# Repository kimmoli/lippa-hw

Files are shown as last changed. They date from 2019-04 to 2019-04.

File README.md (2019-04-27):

LIPPA
=====

* Powering 7.4V 2.5Ah lipo
* PCB Size 80x50 mm, M3 mounting holes at corners 3.5/3.5
* 4 stepper motor drivers
* 3 servo drivers
* CPU STM32
  * UART for Lidar
  * Debug UART
  * USB VCP
  * 3 timers for servo
  * 4 timers for stepper
  * 4 GPIO to control servo directions
  * 4 GPIO to control servo enables
  * 4 GPIO to control servo microstep modes
  * SPI for PS2 controller

Parts
===== 
* CPU [STM32F417VE](http://www.st.com/content/ccc/resource/technical/document/datasheet/98/9f/89/73/01/b1/48/98/DM00035129.pdf/files/DM00035129.pdf/jcr:content/translations/en.DM0003512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)
* Stepper drivers [DRV8834](http://www.ti.com/lit/ds/symlink/drv8834.pdf)
* Power supply [TPS561201](http://www.ti.com/lit/ds/symlink/tps561201.pdf)

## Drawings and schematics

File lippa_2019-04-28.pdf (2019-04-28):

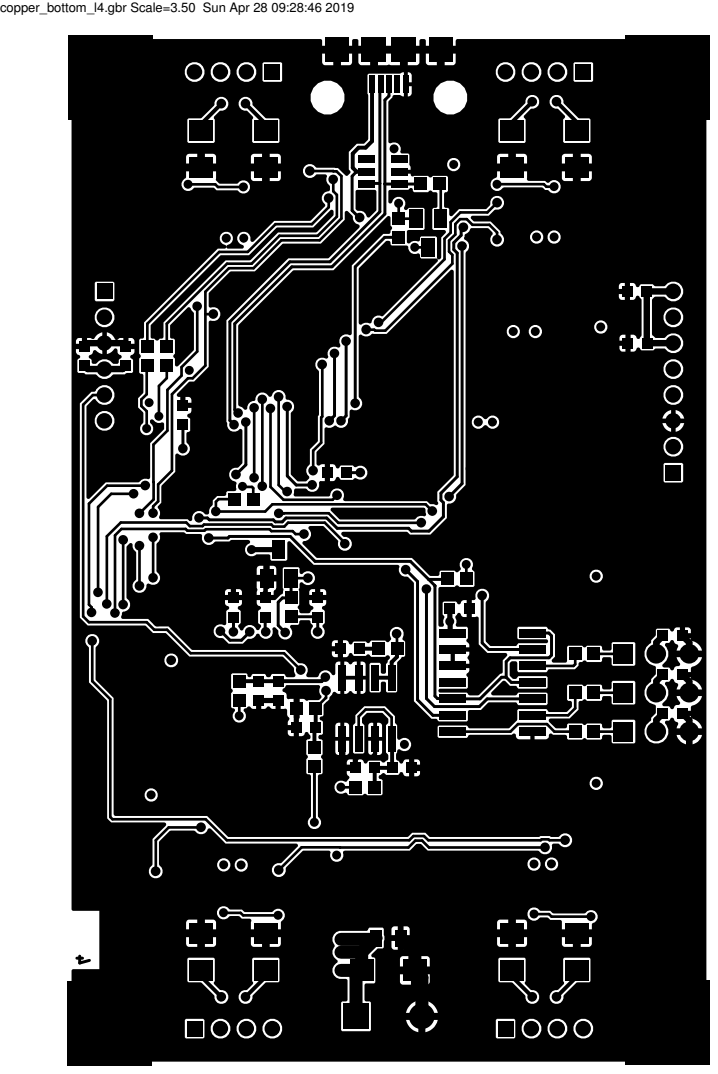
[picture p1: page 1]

copper_bottom_l4.gbr Scale=3.50 Sun Apr 28 09:28:46 2019

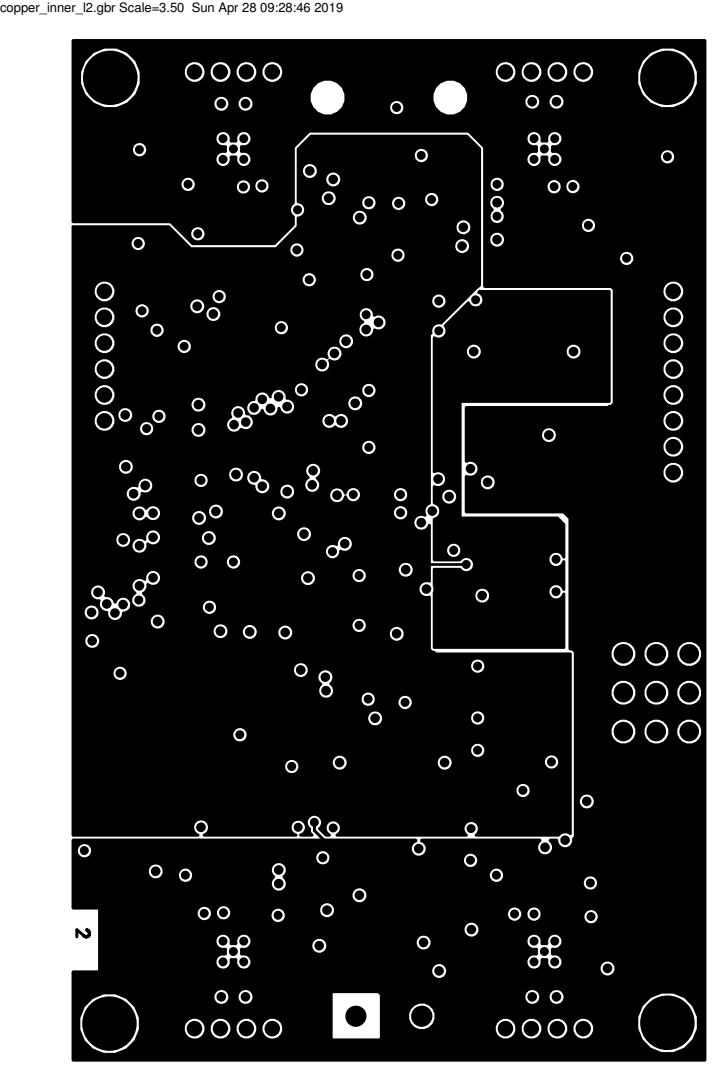
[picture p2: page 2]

copper_inner_l2.gbr Scale=3.50 Sun Apr 28 09:28:46 2019

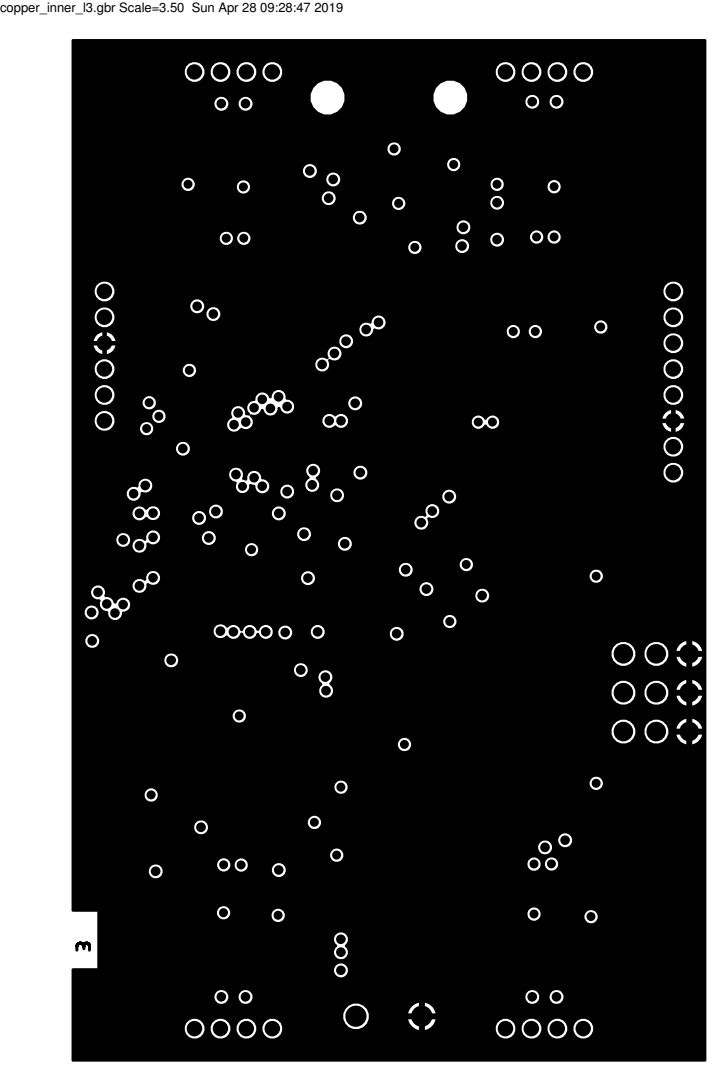
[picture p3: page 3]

copper_inner_l3.gbr Scale=3.50 Sun Apr 28 09:28:47 2019

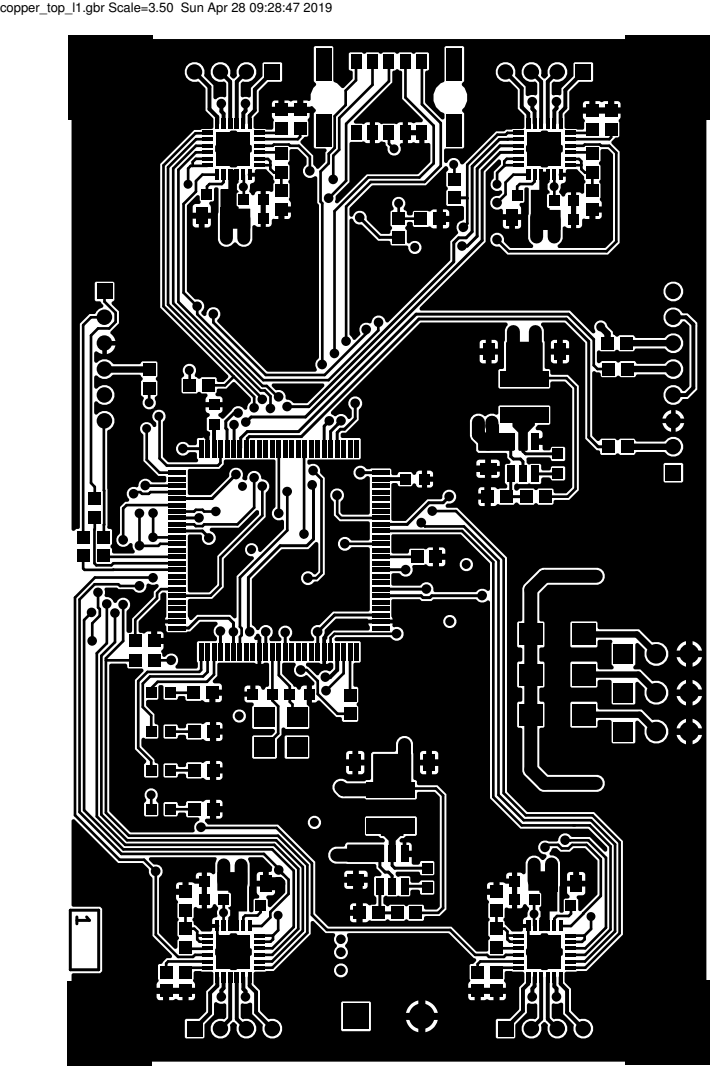
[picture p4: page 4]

copper_top_l1.gbr Scale=3.50 Sun Apr 28 09:28:47 2019

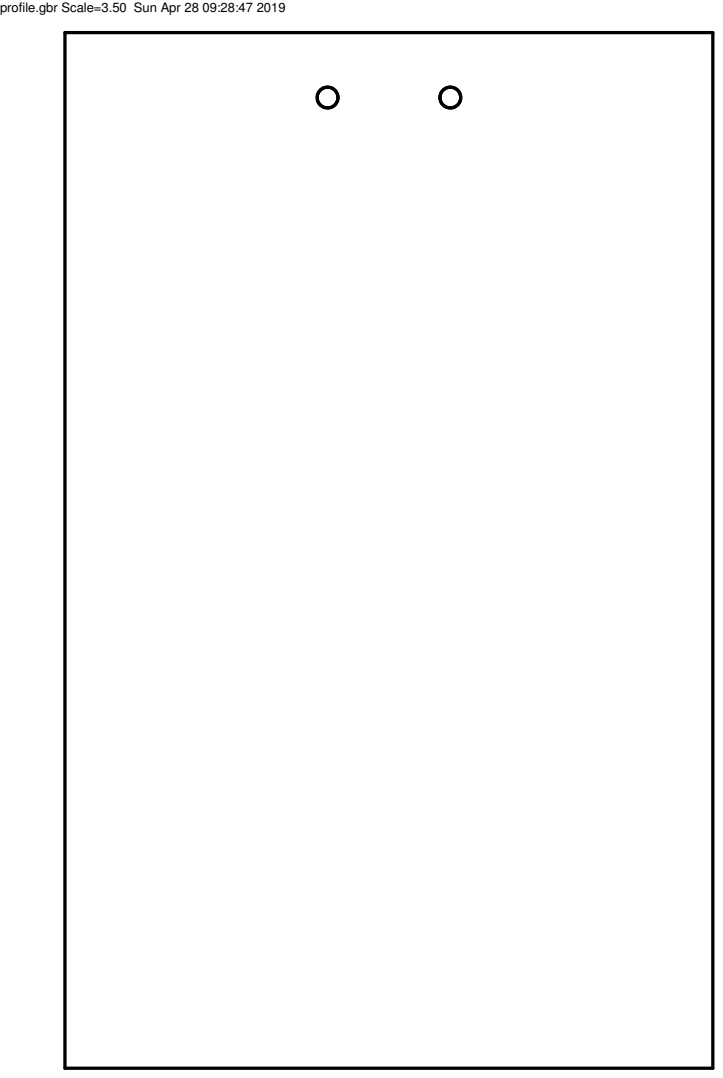
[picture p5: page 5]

profile.gbr Scale=3.50 Sun Apr 28 09:28:47 2019

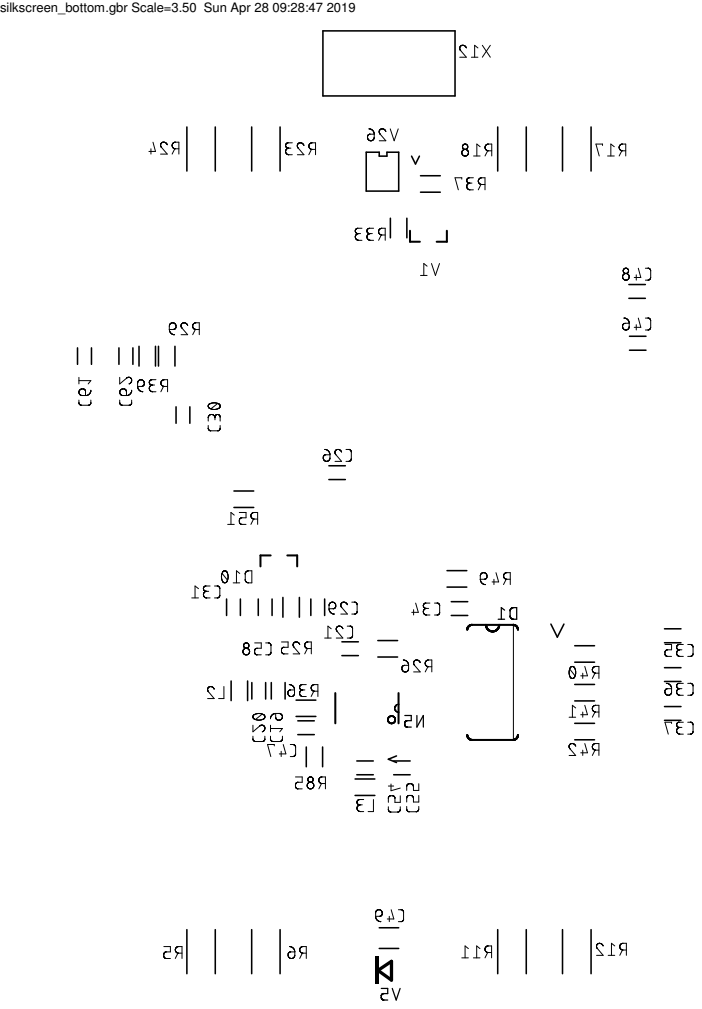
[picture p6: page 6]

silkscreen_bottom.gbr Scale=3.50 Sun Apr 28 09:28:47 2019

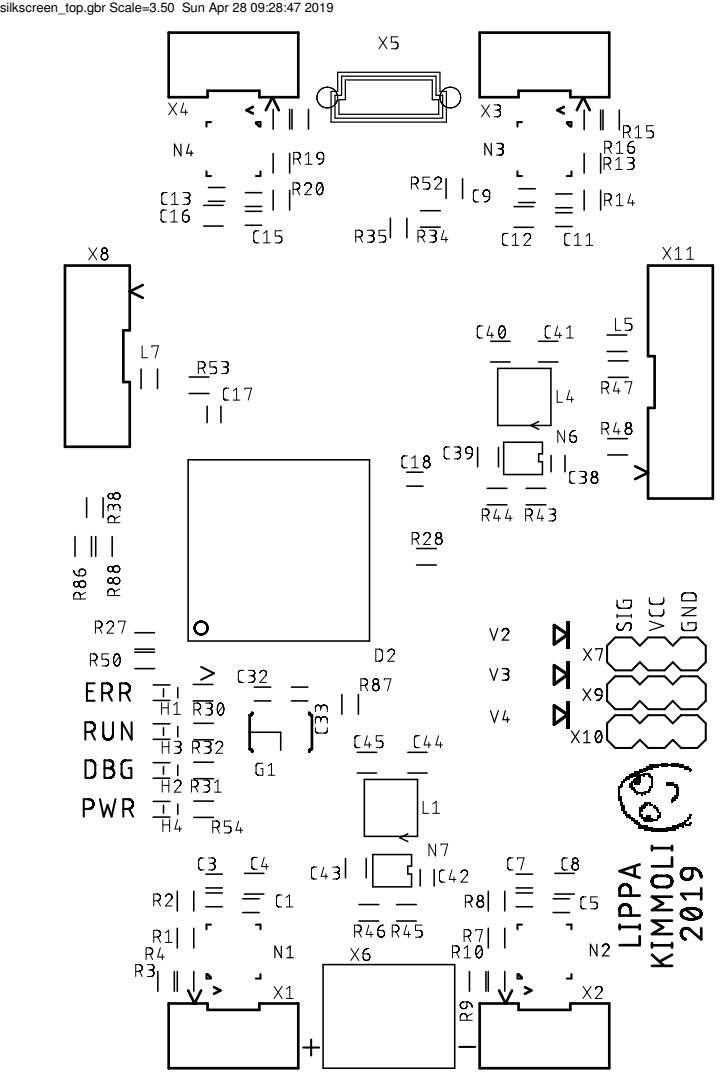
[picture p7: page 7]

silkscreen_top.gbr Scale=3.50 Sun Apr 28 09:28:47 2019

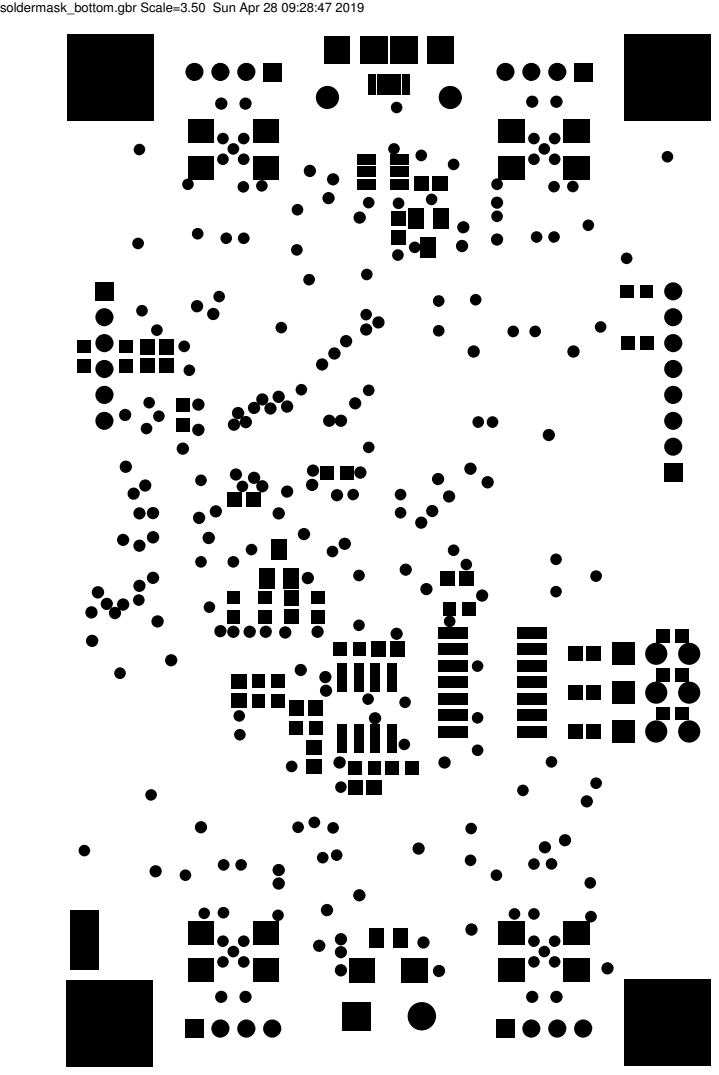
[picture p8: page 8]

soldermask_bottom.gbr Scale=3.50 Sun Apr 28 09:28:47 2019

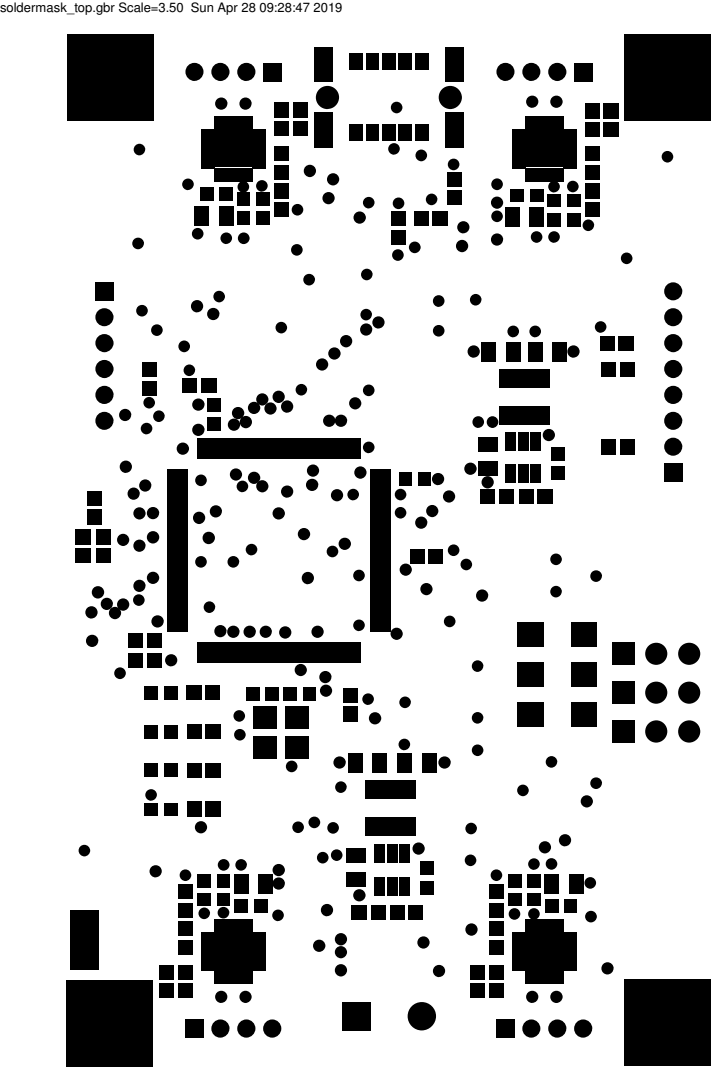
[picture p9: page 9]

soldermask_top.gbr Scale=3.50 Sun Apr 28 09:28:47 2019

solderpaste_bottom.gbr Scale=3.50 Sun Apr 28 09:28:47 2019 solderpaste_top.gbr Scale=3.50 Sun Apr 28 09:28:47 2019

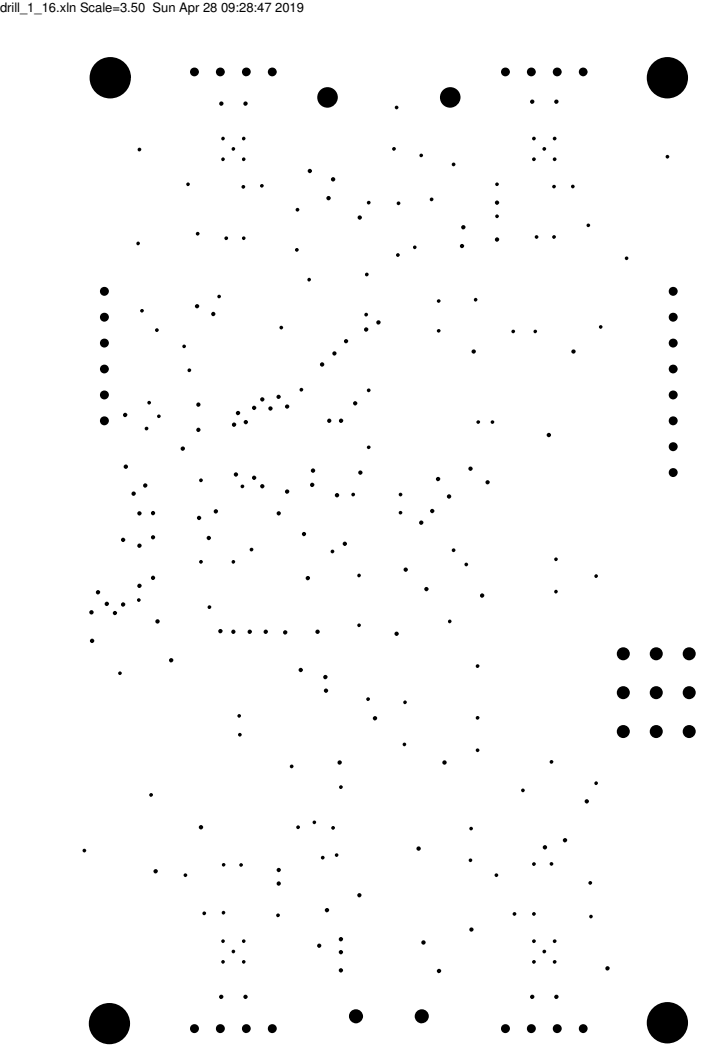
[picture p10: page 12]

drill_1_16.xln Scale=3.50 Sun Apr 28 09:28:47 2019

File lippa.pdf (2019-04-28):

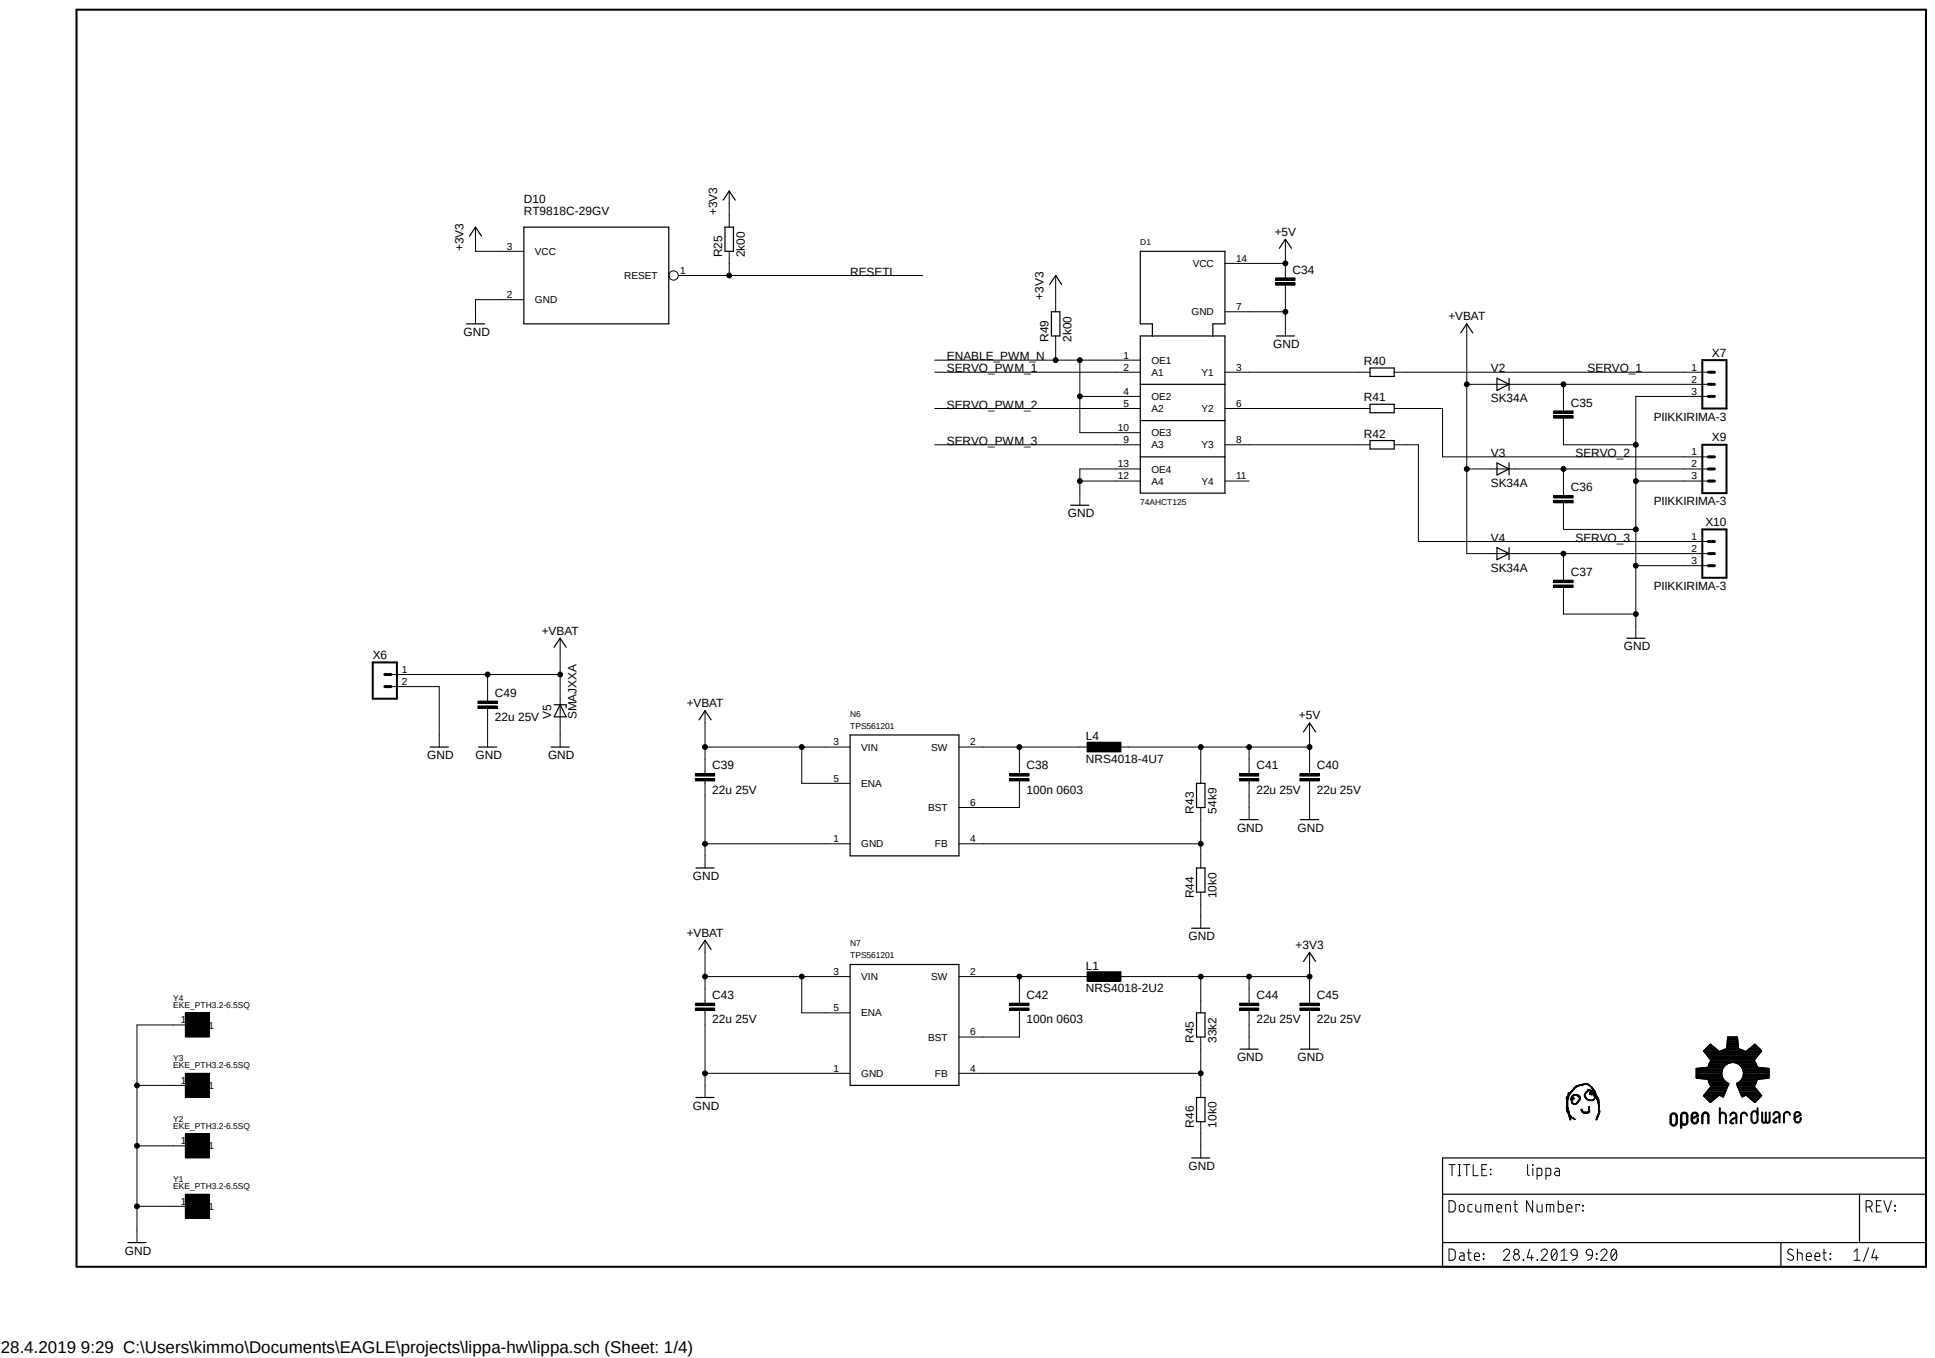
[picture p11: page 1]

28.4.2019 9:29 C:\Users\kimmo\Documents\EAGLE\projects\lippa-hw\lippa.sch (Sheet: 1/4)

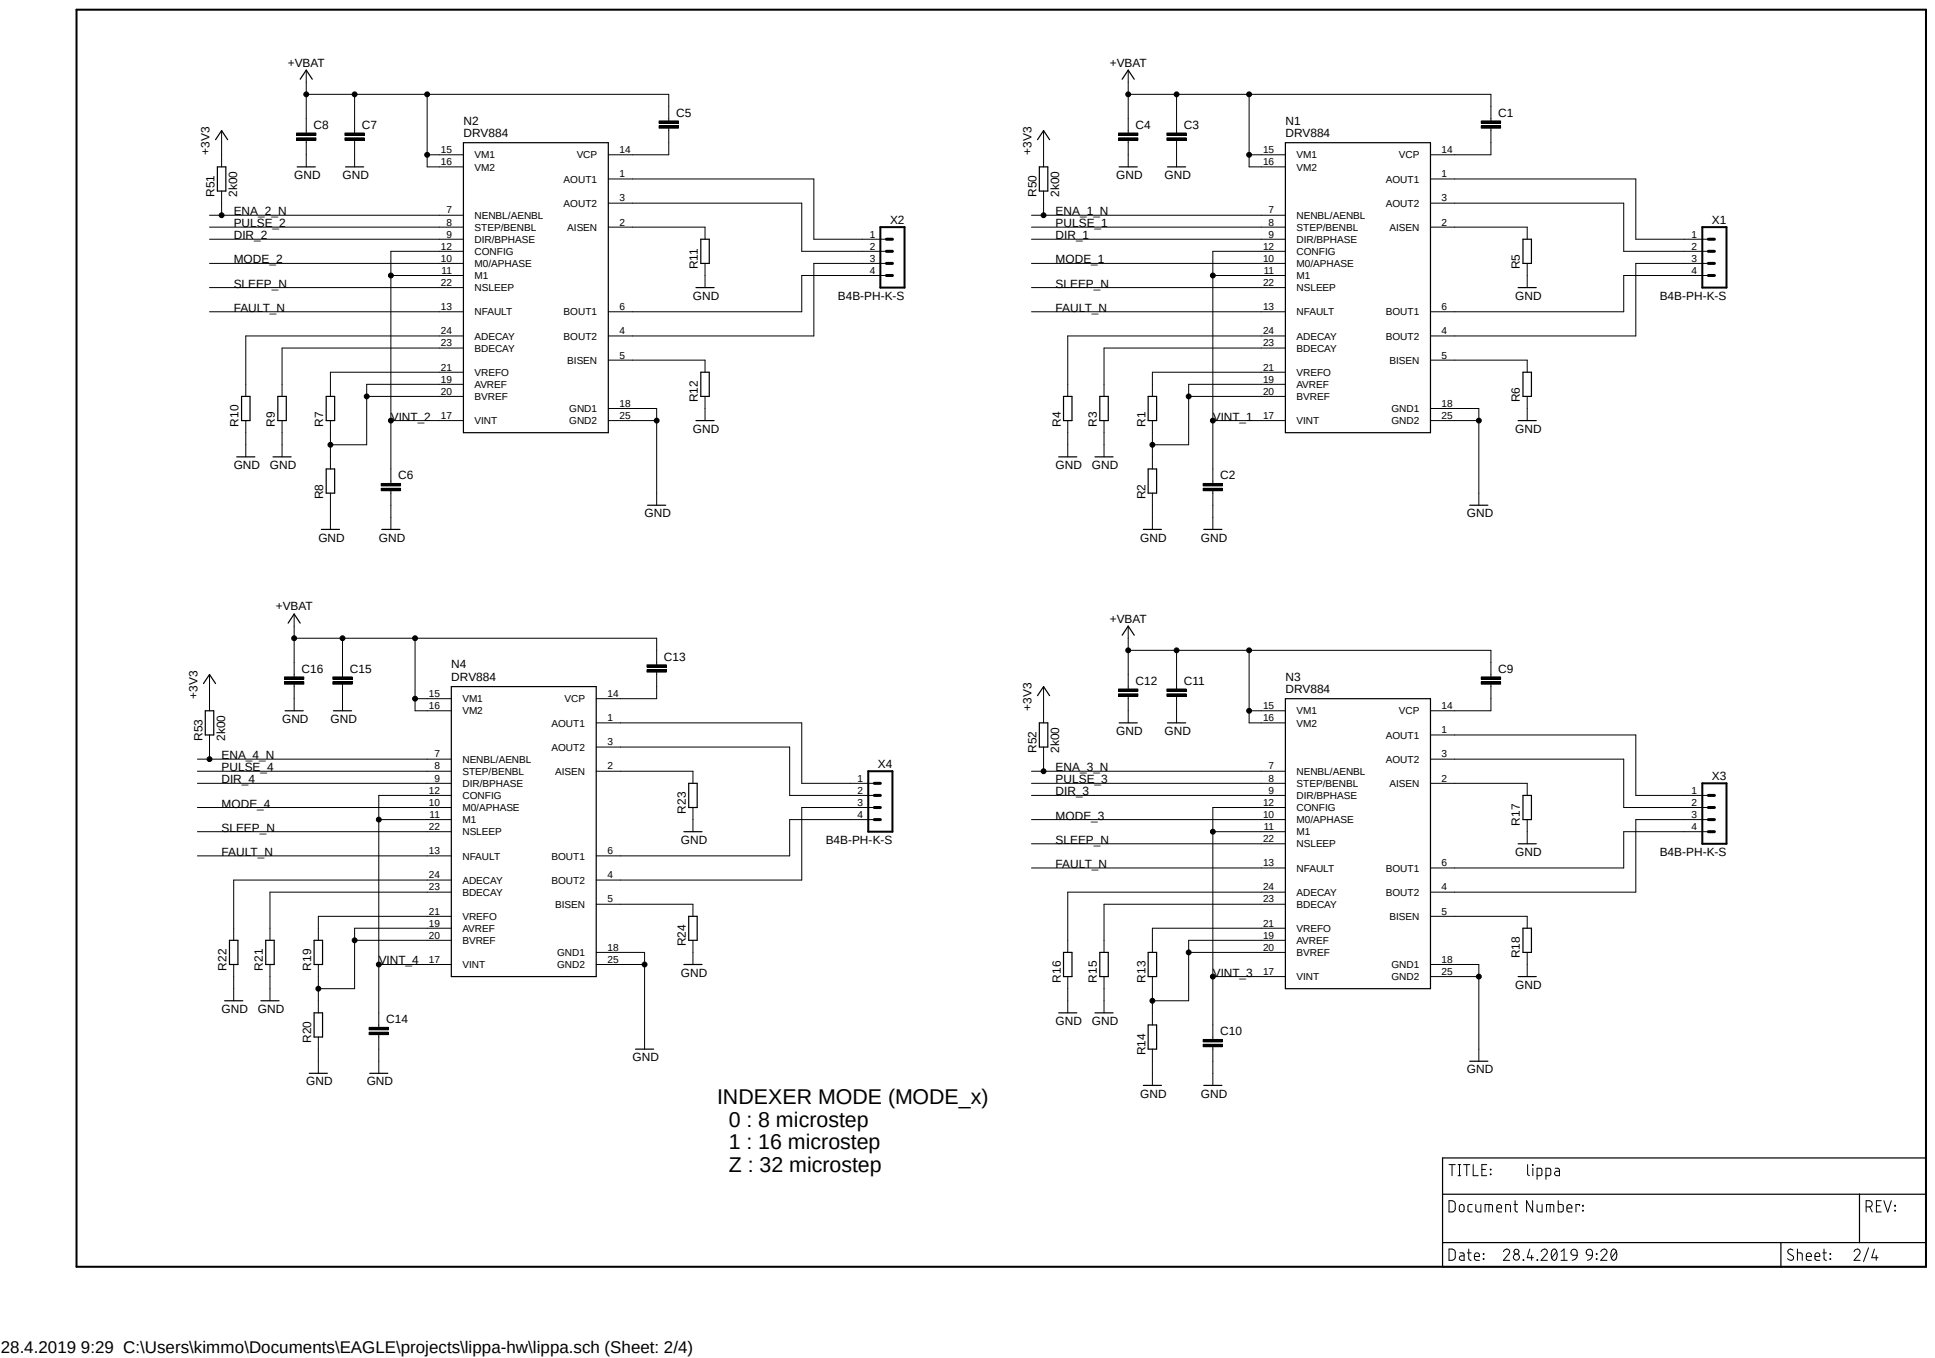
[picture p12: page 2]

BDECAY 23 | 0 : 8 microstep

AVREF 19

VREFO 21

28.4.2019 9:29 C:\Users\kimmo\Documents\EAGLE\projects\lippa-hw\lippa.sch (Sheet: 2/4)


28.4.2019 9:29 C:\Users\kimmo\Documents\EAGLE\projects\lippa-hw\lippa.sch (Sheet: 3/4)


28.4.2019 9:29 C:\Users\kimmo\Documents\EAGLE\projects\lippa-hw\lippa.sch (Sheet: 4/4)

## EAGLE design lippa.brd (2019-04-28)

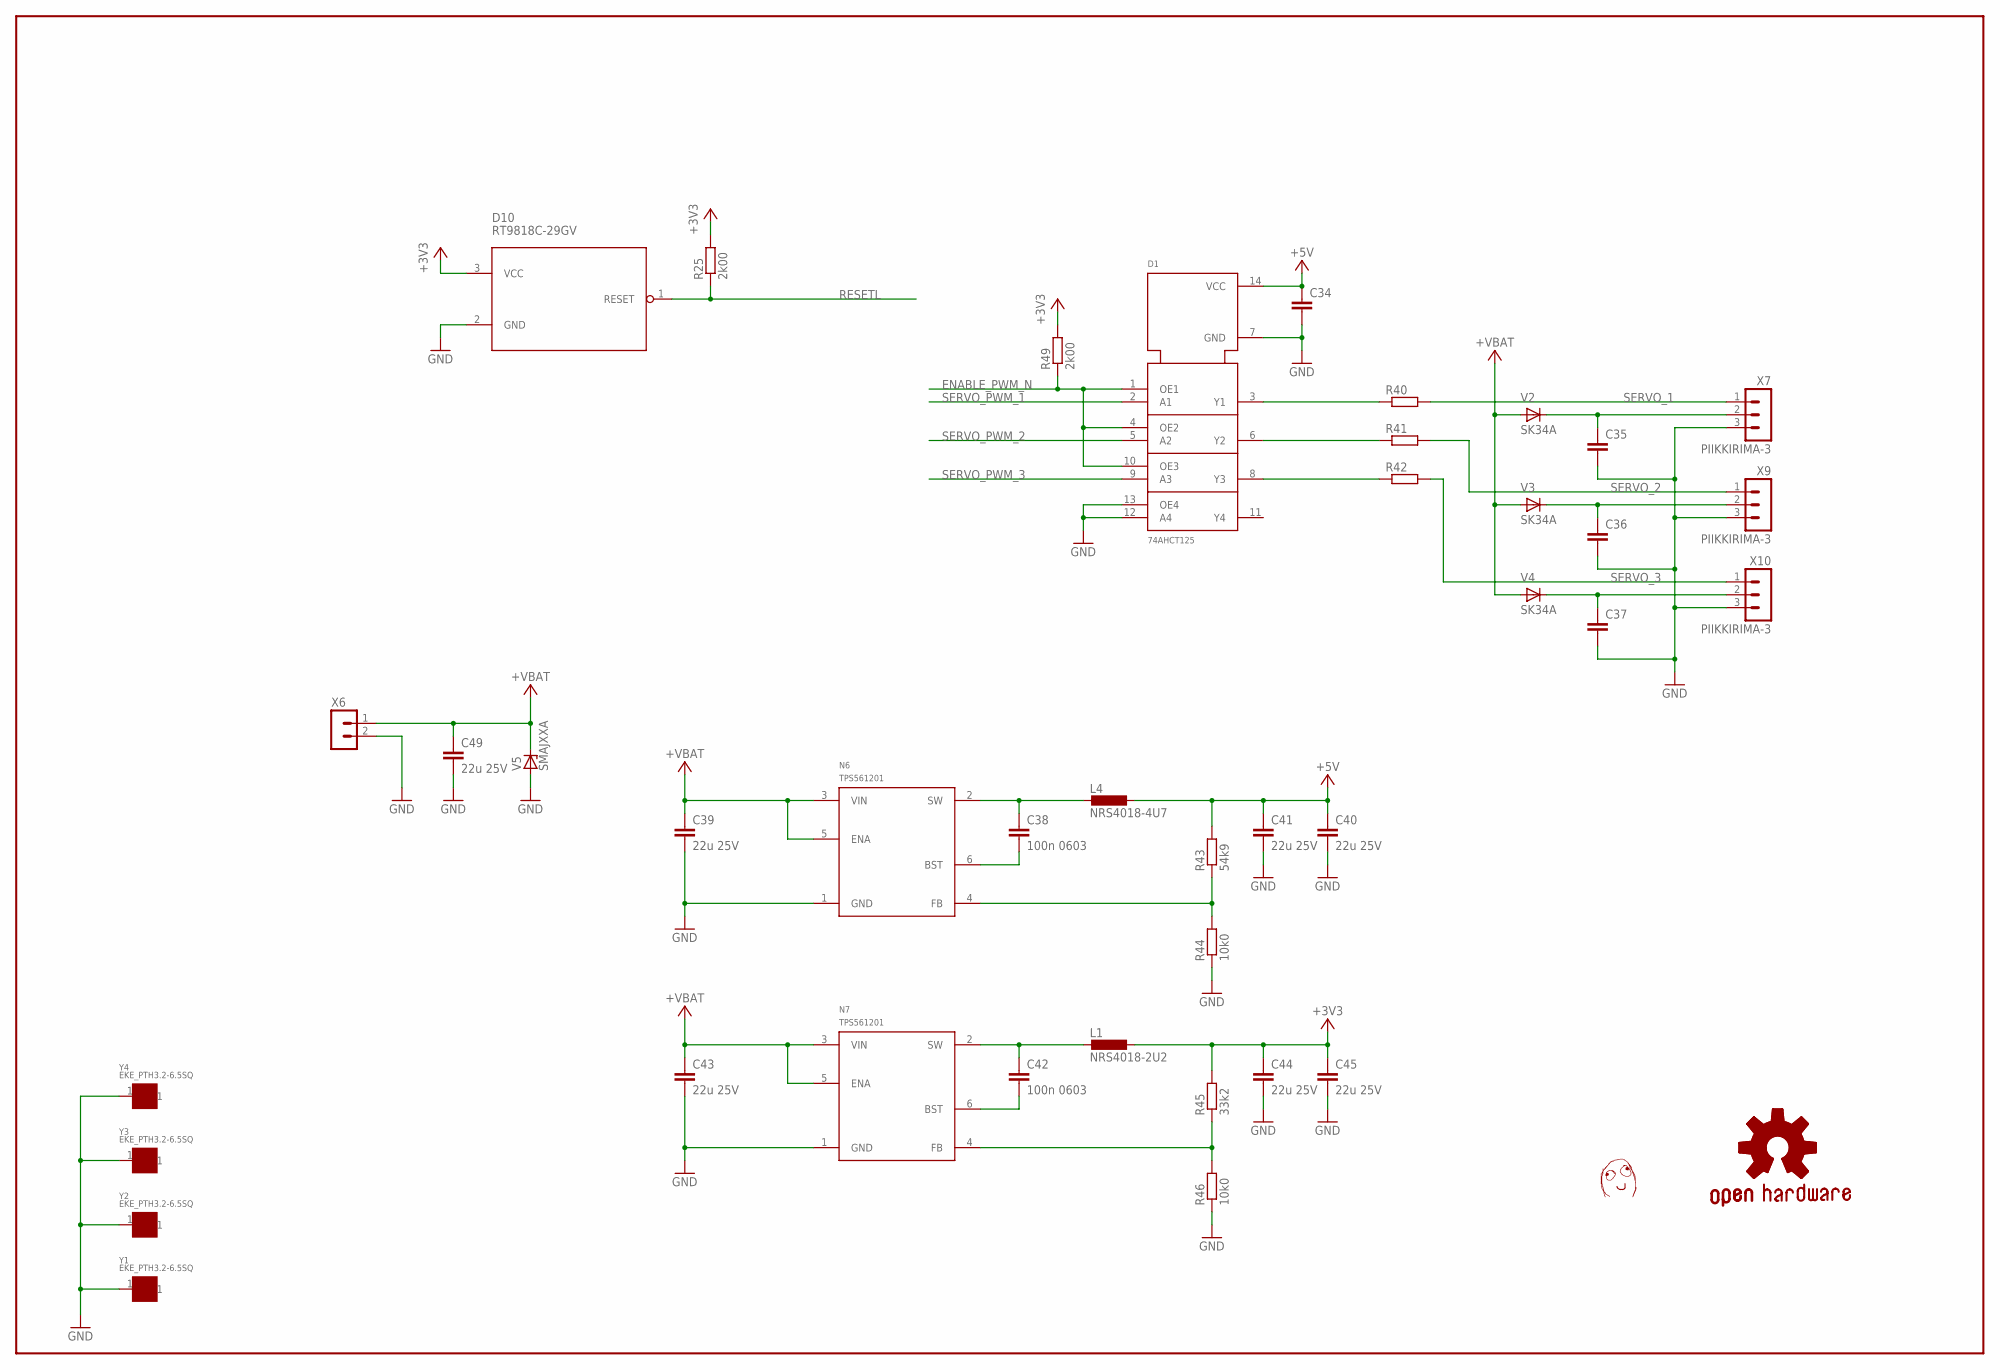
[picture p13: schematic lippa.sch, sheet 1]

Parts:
C34, C35, C36, C37: OMAT_IC_2_CAP0603; OMAT_IC_2_C0603
C38, C42: 100n 0603; OMAT_IC_2_C0603
C39, C40, C41, C43, C44, C45, C49: 22u 25V; OMAT_IC_2_C0805
D1: 74AHCT125; SO14
D10: RT9818C-29GV; SOT23
L1: NRS4018-2U2; NRS4018
L4: NRS4018-4U7; NRS4018
N6, N7: TPS561201; OMAT_IC_2_SOT23-6
R25, R49: 2k00; R0603
R40, R41, R42: OMAT_IC_2_RES0603; OMAT_IC_2_R0603
R43: 54k9; OMAT_IC_2_R0603
R44, R46: 10k0; OMAT_IC_2_R0603
R45: 33k2; OMAT_IC_2_R0603
U$1: DAFUG
V2, V3, V4: SK34A; OMAT_IC_2_DO214AC
V5: SMAJXXA; DO214AC
X6: TE_RUUVILIITIN2
X7, X9, X10: PIIKKIRIMA-3
Y1, Y2, Y3, Y4: EKE_PTH3.2-6.5SQ; EKE_PTH-3.2-6.5SQ

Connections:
+3V3: C44.1, C45.1, D10.3 (VCC), L1.1, R25.2, R45.2, R49.2; also elsewhere on the board
+5V: C34.1, C40.1, C41.1, D1.14 (VCC), L4.1, R43.2; also elsewhere on the board
+VBAT: C39.1, C43.1, C49.1, N6.3 (VIN), N6.5 (ENA), N7.3 (VIN), N7.5 (ENA), V2.A, V3.A, V4.A, V5.C, X6.1; also elsewhere on the board
ENABLE_PWM_N: D1.1 (OE1), D1.4 (OE2), D1.10 (OE3), R49.1; also elsewhere on the board
GND: C34.2, C35.2, C36.2, C37.2, C39.2, C40.2, C41.2, C43.2, C44.2, C45.2, C49.2, D1.7 (GND), D1.12 (A4), D1.13 (OE4), D10.2 (GND), N6.1 (GND), N7.1 (GND), R44.1, R46.1, V5.A, X6.2, X7.3, X9.3, X10.3, Y1.1, Y2.1, Y3.1, Y4.1; also elsewhere on the board
unnamed: D1.3 (Y1), R40.1
unnamed: D1.6 (Y2), R41.1
unnamed: D1.8 (Y3), R42.1
unnamed: C38.1, L4.2, N6.2 (SW)
unnamed: C37.1, V4.C, X10.2
unnamed: C36.1, V3.C, X9.2
unnamed: C35.1, V2.C, X7.2
unnamed: C38.2, N6.6 (BST)
unnamed: N6.4 (FB), R43.1, R44.2
unnamed: C42.1, L1.2, N7.2 (SW)
unnamed: C42.2, N7.6 (BST)
unnamed: N7.4 (FB), R45.1, R46.2
RESETL: D10.1 (RESET), R25.1; also elsewhere on the board
SERVO_1: R40.2, X7.1
SERVO_2: R41.2, X9.1
SERVO_3: R42.2, X10.1
SERVO_PWM_1: D1.2 (A1); also elsewhere on the board
SERVO_PWM_2: D1.5 (A2); also elsewhere on the board
SERVO_PWM_3: D1.9 (A3); also elsewhere on the board

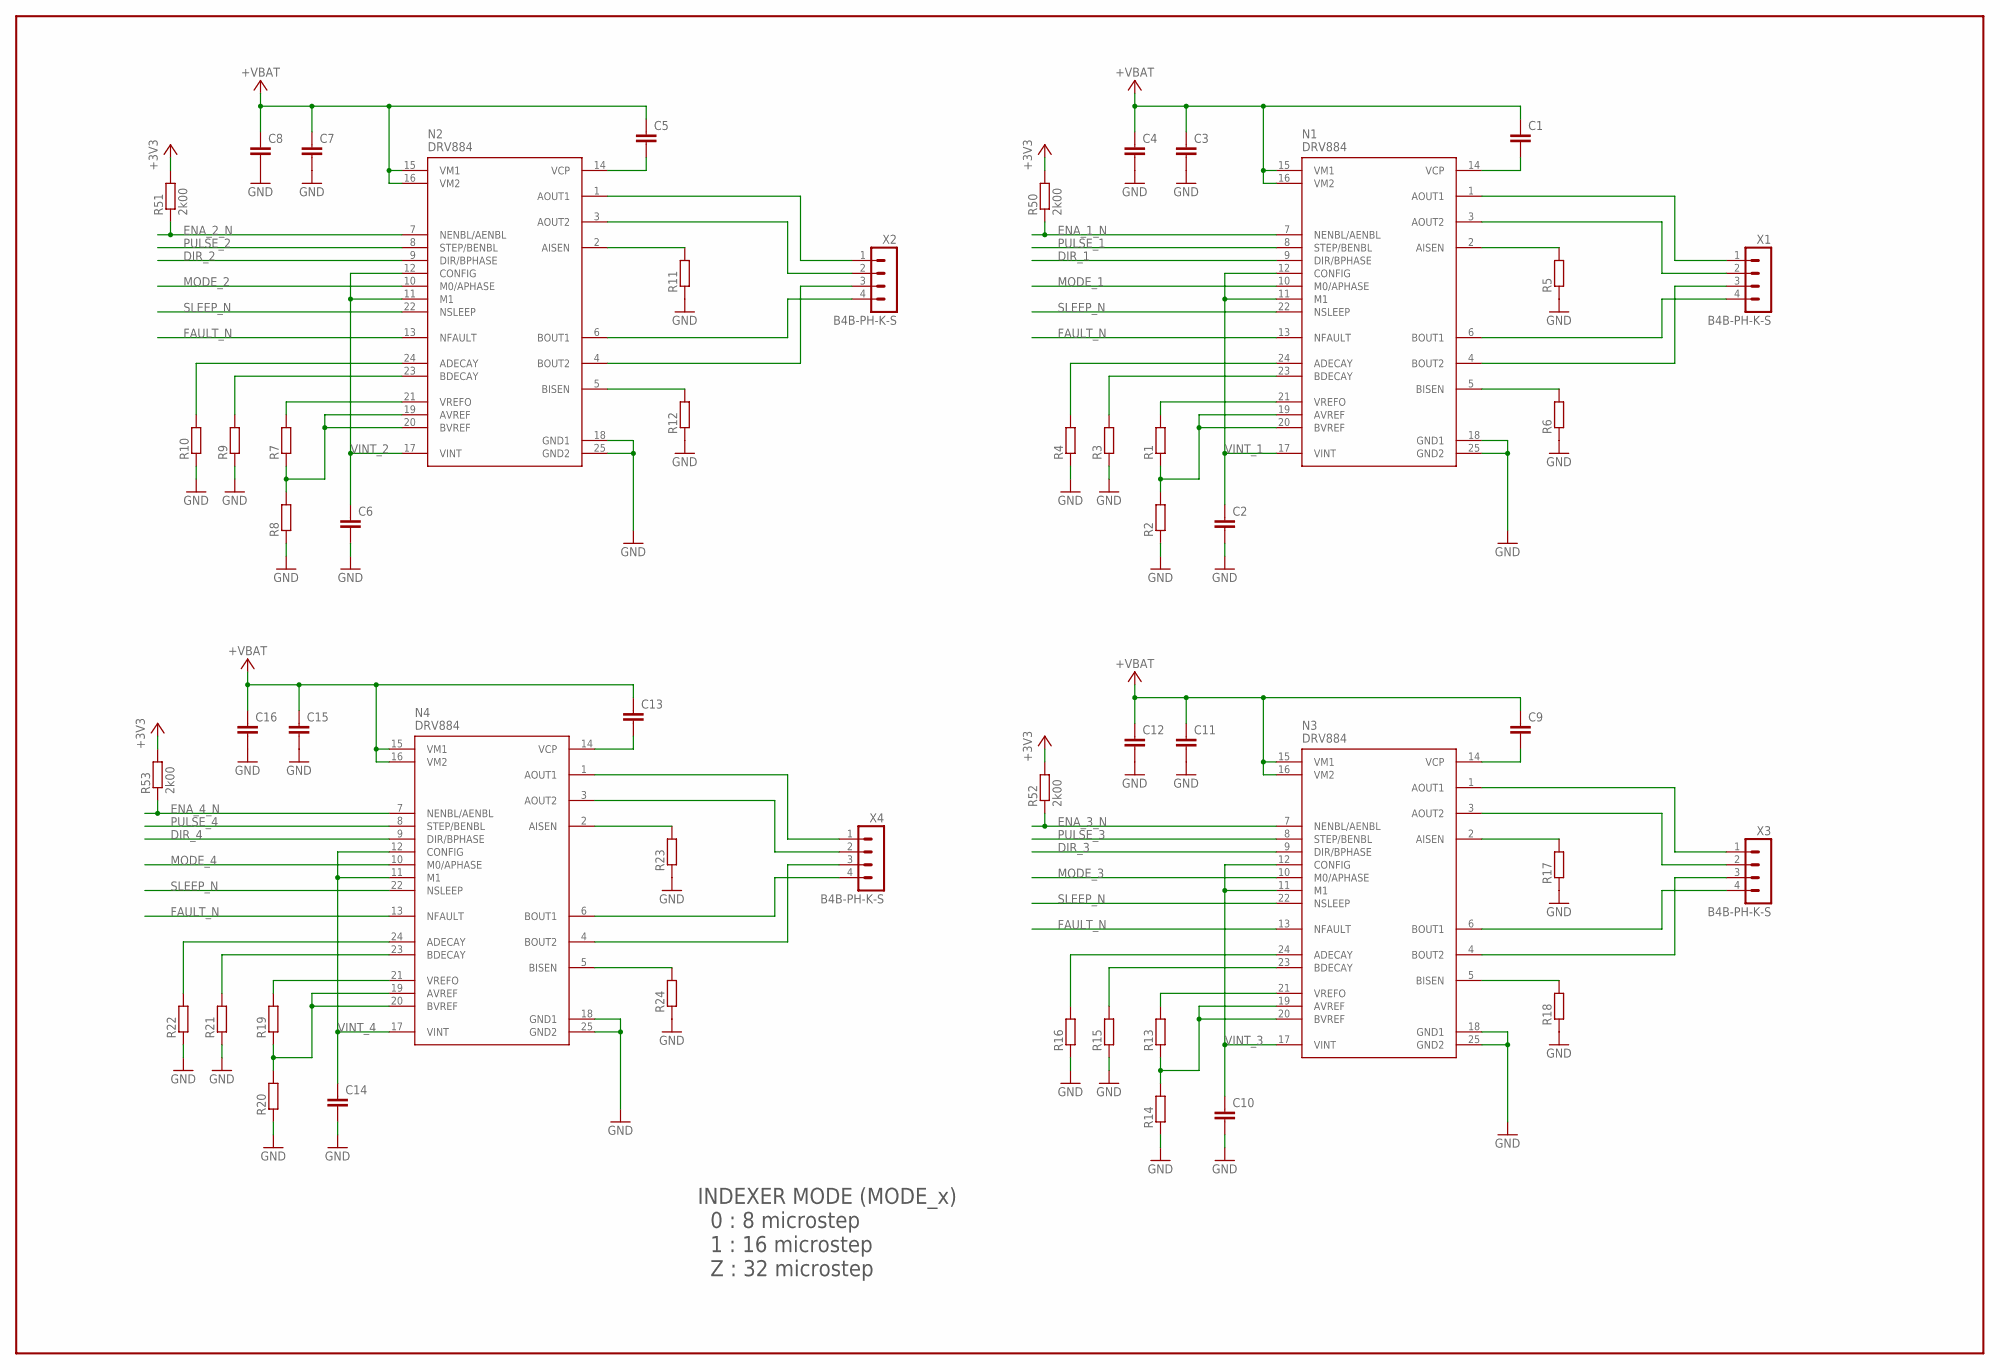
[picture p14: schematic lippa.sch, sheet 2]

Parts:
C1, C2, C3, C5, C6, C7, C9, C10, C11, C13, C14, C15: OMAT_IC_2_CAP0603; OMAT_IC_2_C0603
C4, C8, C12, C16: OMAT_IC_2_CAP0805; OMAT_IC_2_C0805
N1, N2, N3, N4: DRV884; QFN50P400X400X100-25N
R1, R2, R3, R4, R7, R8, R9, R10, R13, R14, R15, R16, R19, R20, R21, R22: OMAT_IC_2_RES0603; OMAT_IC_2_R0603
R5, R6, R11, R12, R17, R18, R23, R24: OMAT_IC_2_RES1206; OMAT_IC_2_R1206
R50, R51, R52, R53: 2k00; R0603
X1, X2, X3, X4: B4B-PH-K-S

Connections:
+3V3: R50.2, R51.2, R52.2, R53.2; also elsewhere on the board
+VBAT: C1.1, C3.1, C4.1, C5.1, C7.1, C8.1, C9.1, C11.1, C12.1, C13.1, C15.1, C16.1, N1.15 (VM1), N1.16 (VM2), N2.15 (VM1), N2.16 (VM2), N3.15 (VM1), N3.16 (VM2), N4.15 (VM1), N4.16 (VM2); also elsewhere on the board
DIR_1: N1.9 (DIR/BPHASE); also elsewhere on the board
DIR_2: N2.9 (DIR/BPHASE); also elsewhere on the board
DIR_3: N3.9 (DIR/BPHASE); also elsewhere on the board
DIR_4: N4.9 (DIR/BPHASE); also elsewhere on the board
ENA_1_N: N1.7 (NENBL/AENBL), R50.1; also elsewhere on the board
ENA_2_N: N2.7 (NENBL/AENBL), R51.1; also elsewhere on the board
ENA_3_N: N3.7 (NENBL/AENBL), R52.1; also elsewhere on the board
ENA_4_N: N4.7 (NENBL/AENBL), R53.1; also elsewhere on the board
FAULT_N: N1.13 (NFAULT), N2.13 (NFAULT), N3.13 (NFAULT), N4.13 (NFAULT); also elsewhere on the board
GND: C2.2, C3.2, C4.2, C6.2, C7.2, C8.2, C10.2, C11.2, C12.2, C14.2, C15.2, C16.2, N1.18 (GND1), N1.25 (GND2), N2.18 (GND1), N2.25 (GND2), N3.18 (GND1), N3.25 (GND2), N4.18 (GND1), N4.25 (GND2), R2.1, R3.1, R4.1, R5.1, R6.1, R8.1, R9.1, R10.1, R11.1, R12.1, R14.1, R15.1, R16.1, R17.1, R18.1, R20.1, R21.1, R22.1, R23.1, R24.1; also elsewhere on the board
MODE_1: N1.10 (M0/APHASE); also elsewhere on the board
MODE_2: N2.10 (M0/APHASE); also elsewhere on the board
MODE_3: N3.10 (M0/APHASE); also elsewhere on the board
MODE_4: N4.10 (M0/APHASE); also elsewhere on the board
unnamed: C1.2, N1.14 (VCP)
unnamed: N1.24 (ADECAY), R4.2
unnamed: N1.21 (VREFO), R1.2
unnamed: N1.19 (AVREF), N1.20 (BVREF), R1.1, R2.2
unnamed: N1.23 (BDECAY), R3.2
unnamed: N1.2 (AISEN), R5.2
unnamed: N1.5 (BISEN), R6.2
unnamed: N1.6 (BOUT1), X1.4
unnamed: N1.4 (BOUT2), X1.3
unnamed: N1.1 (AOUT1), X1.1
unnamed: N1.3 (AOUT2), X1.2
unnamed: C5.2, N2.14 (VCP)
unnamed: N2.21 (VREFO), R7.2
unnamed: N2.19 (AVREF), N2.20 (BVREF), R7.1, R8.2
unnamed: N2.24 (ADECAY), R10.2
unnamed: N2.23 (BDECAY), R9.2
unnamed: N2.2 (AISEN), R11.2
unnamed: N2.5 (BISEN), R12.2
unnamed: N2.6 (BOUT1), X2.4
unnamed: N2.4 (BOUT2), X2.3
unnamed: N2.1 (AOUT1), X2.1
unnamed: N2.3 (AOUT2), X2.2
unnamed: C9.2, N3.14 (VCP)
unnamed: N3.21 (VREFO), R13.2
unnamed: N3.19 (AVREF), N3.20 (BVREF), R13.1, R14.2
unnamed: N3.24 (ADECAY), R16.2
unnamed: N3.23 (BDECAY), R15.2
unnamed: N3.2 (AISEN), R17.2
unnamed: N3.5 (BISEN), R18.2
unnamed: N3.6 (BOUT1), X3.4
unnamed: N3.4 (BOUT2), X3.3
unnamed: N3.1 (AOUT1), X3.1
unnamed: N3.3 (AOUT2), X3.2
unnamed: C13.2, N4.14 (VCP)
unnamed: N4.21 (VREFO), R19.2
unnamed: N4.19 (AVREF), N4.20 (BVREF), R19.1, R20.2
unnamed: N4.24 (ADECAY), R22.2
unnamed: N4.23 (BDECAY), R21.2
unnamed: N4.2 (AISEN), R23.2
unnamed: N4.5 (BISEN), R24.2
unnamed: N4.6 (BOUT1), X4.4
unnamed: N4.4 (BOUT2), X4.3
unnamed: N4.1 (AOUT1), X4.1
unnamed: N4.3 (AOUT2), X4.2
PULSE_1: N1.8 (STEP/BENBL); also elsewhere on the board
PULSE_2: N2.8 (STEP/BENBL); also elsewhere on the board
PULSE_3: N3.8 (STEP/BENBL); also elsewhere on the board
PULSE_4: N4.8 (STEP/BENBL); also elsewhere on the board
SLEEP_N: N1.22 (NSLEEP), N2.22 (NSLEEP), N3.22 (NSLEEP), N4.22 (NSLEEP); also elsewhere on the board
VINT_1: C2.1, N1.11 (M1), N1.12 (CONFIG), N1.17 (VINT)
VINT_2: C6.1, N2.11 (M1), N2.12 (CONFIG), N2.17 (VINT)
VINT_3: C10.1, N3.11 (M1), N3.12 (CONFIG), N3.17 (VINT)
VINT_4: C14.1, N4.11 (M1), N4.12 (CONFIG), N4.17 (VINT)

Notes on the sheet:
INDEXER MODE (MODE_x) 0 : 8 microstep 1 : 16 microstep Z : 32 microstep

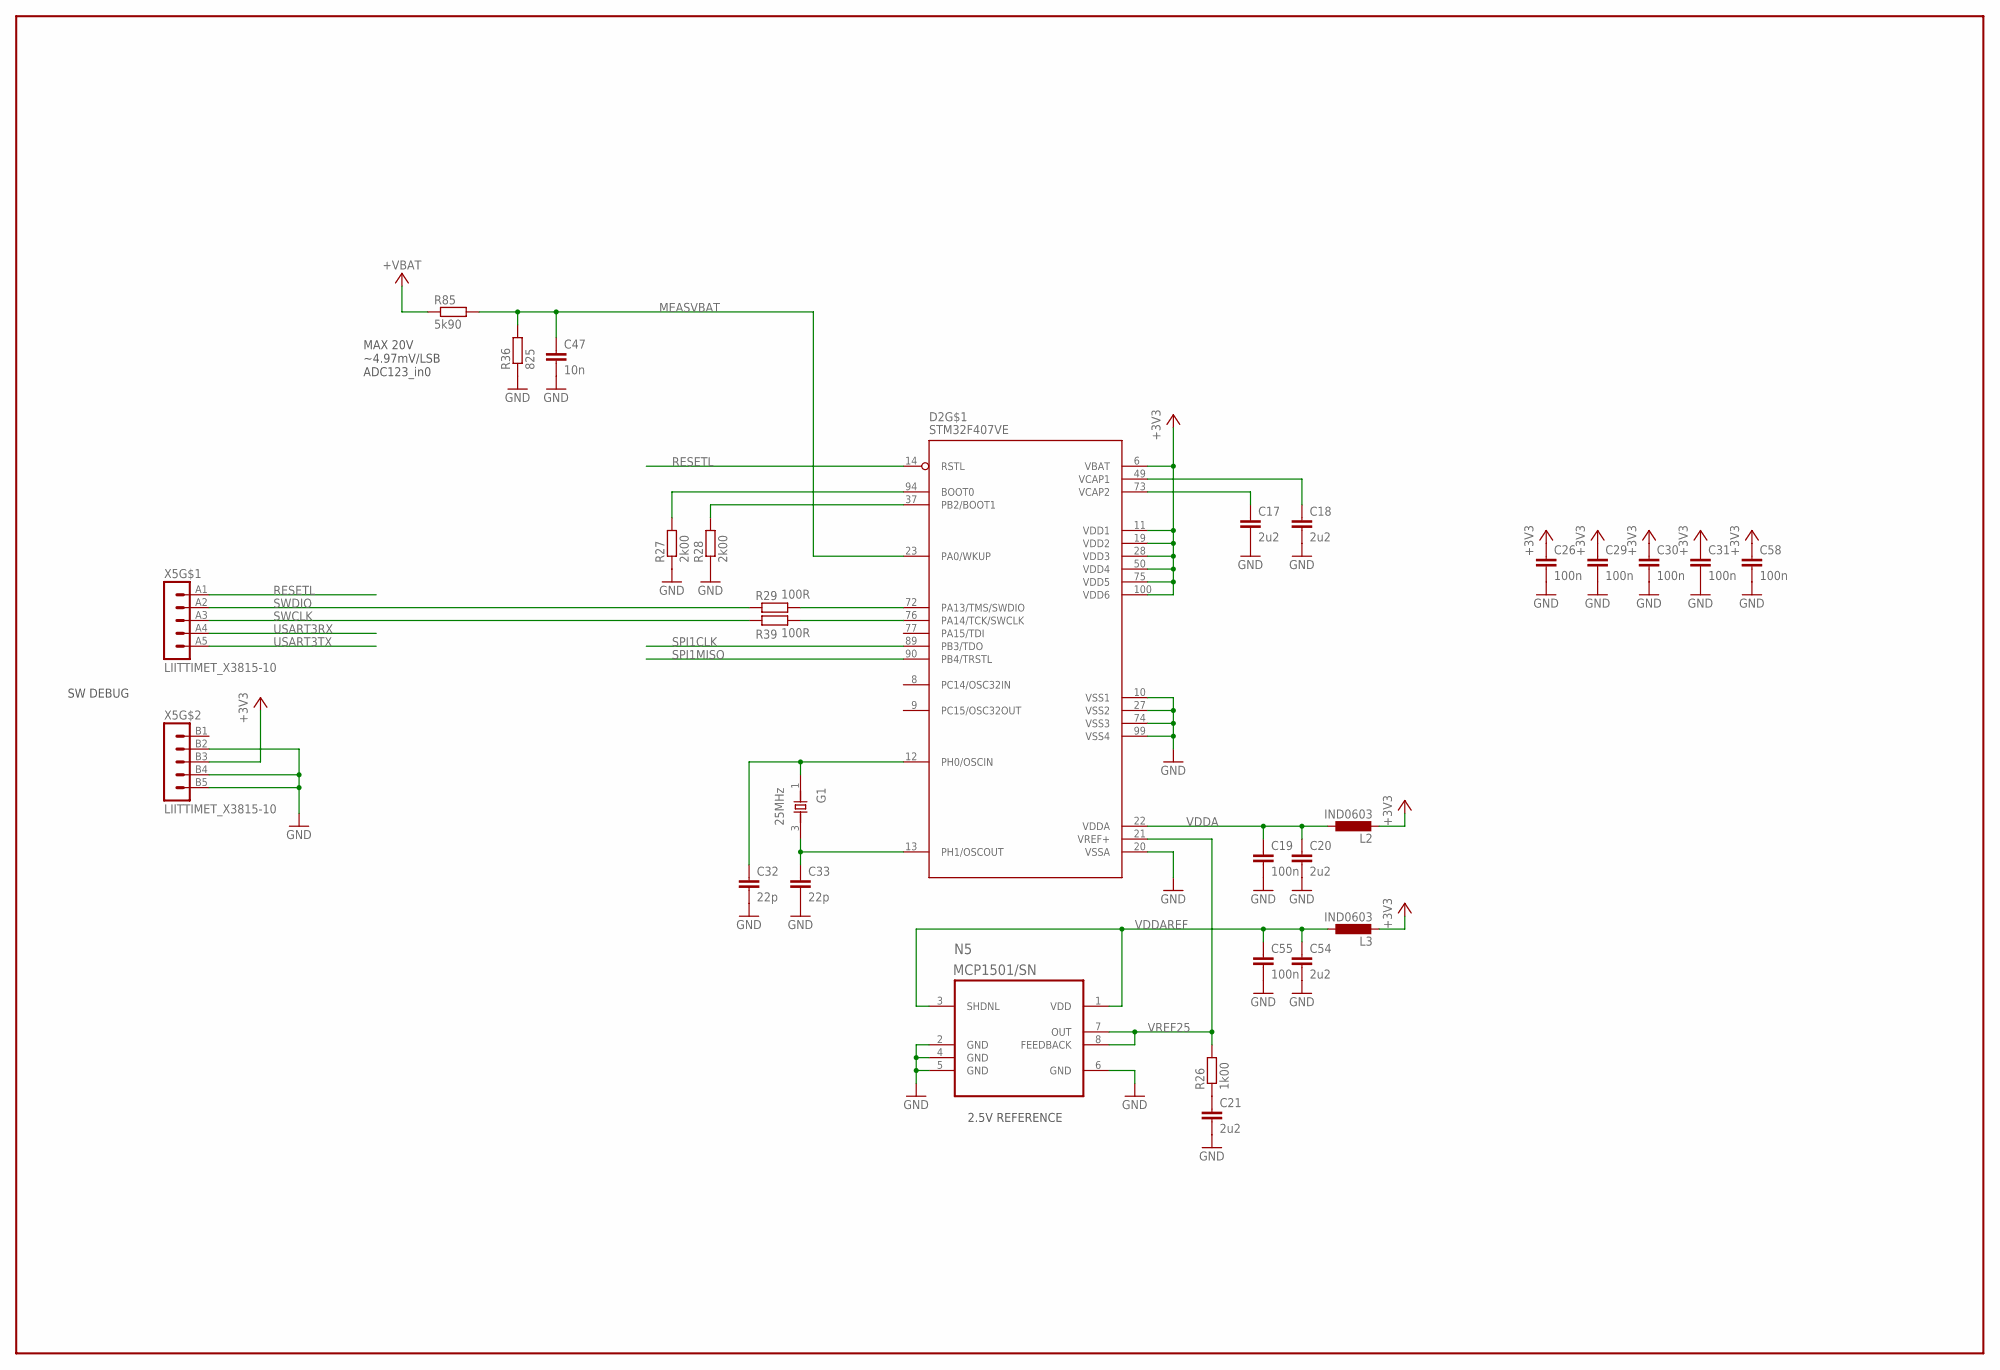
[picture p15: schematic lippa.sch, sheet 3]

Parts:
C17, C18, C20, C21, C54: 2u2; C0603
C19, C26, C29, C30, C31, C55, C58: 100n; C0603
C32, C33: 22p; C0603
C47: 10n; C0603
D2: STM32F407VE; LQFP-100
G1: 25MHz; X_3225
L2, L3: IND0603; R0603
N5: MCP1501/SN; SOIC8-N_MC
R26: 1k00; R0603
R27, R28: 2k00; R0603
R29, R39: 100R; PASSIIVIT_R0603
R36: 825; R0603
R85: 5k90; R0603
X5: LIITTIMET_X3815-10; LIITTIMET_15110102601

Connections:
+3V3: C26.1, C29.1, C30.1, C31.1, C58.1, D2.6 (VBAT), D2.11 (VDD1), D2.19 (VDD2), D2.28 (VDD3), D2.50 (VDD4), D2.75 (VDD5), D2.100 (VDD6), L2.2, L3.2, X5.B3 (3); also elsewhere on the board
+VBAT: R85.1; also elsewhere on the board
BOOT0: D2.94 (BOOT0), R27.2
BOOT1: D2.37 (PB2/BOOT1), R28.2
GND: C17.2, C18.2, C19.2, C20.2, C21.2, C26.2, C29.2, C30.2, C31.2, C32.2, C33.2, C47.2, C54.2, C55.2, C58.2, D2.10 (VSS1), D2.20 (VSSA), D2.27 (VSS2), D2.74 (VSS3), D2.99 (VSS4), N5.2 (GND), N5.4 (GND), N5.5 (GND), N5.6 (GND), R27.1, R28.1, R36.1, X5.B2 (2), X5.B4 (4), X5.B5 (5); also elsewhere on the board
MEASVBAT: C47.1, D2.23 (PA0/WKUP), R36.2, R85.2
unnamed: C21.1, R26.1
OSCIN: C32.1, D2.12 (PH0/OSCIN), G1.1 (X1)
OSCOUT: C33.1, D2.13 (PH1/OSCOUT), G1.3 (X2)
RESETL: D2.14 (RSTL), X5.A1 (1); also elsewhere on the board
SPI1CLK: D2.89 (PB3/TDO); also elsewhere on the board
SPI1MISO: D2.90 (PB4/TRSTL); also elsewhere on the board
SWCLK: R39.1, X5.A3 (3)
SWCLK_CPU: D2.76 (PA14/TCK/SWCLK), R39.2
SWDIO: R29.1, X5.A2 (2)
SWDIO_CPU: D2.72 (PA13/TMS/SWDIO), R29.2
USART3RX: X5.A4 (4); also elsewhere on the board
USART3TX: X5.A5 (5); also elsewhere on the board
VCAP1: C18.1, D2.49 (VCAP1)
VCAP2: C17.1, D2.73 (VCAP2)
VDDA: C19.1, C20.1, D2.22 (VDDA), L2.1
VDDAREF: C54.1, C55.1, L3.1, N5.1 (VDD), N5.3 (SHDNL)
VREF25: D2.21 (VREF+), N5.7 (OUT), N5.8 (FEEDBACK), R26.2

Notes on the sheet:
2.5V REFERENCE
SW DEBUG
MAX 20V ~4.97mV/LSB ADC123_in0

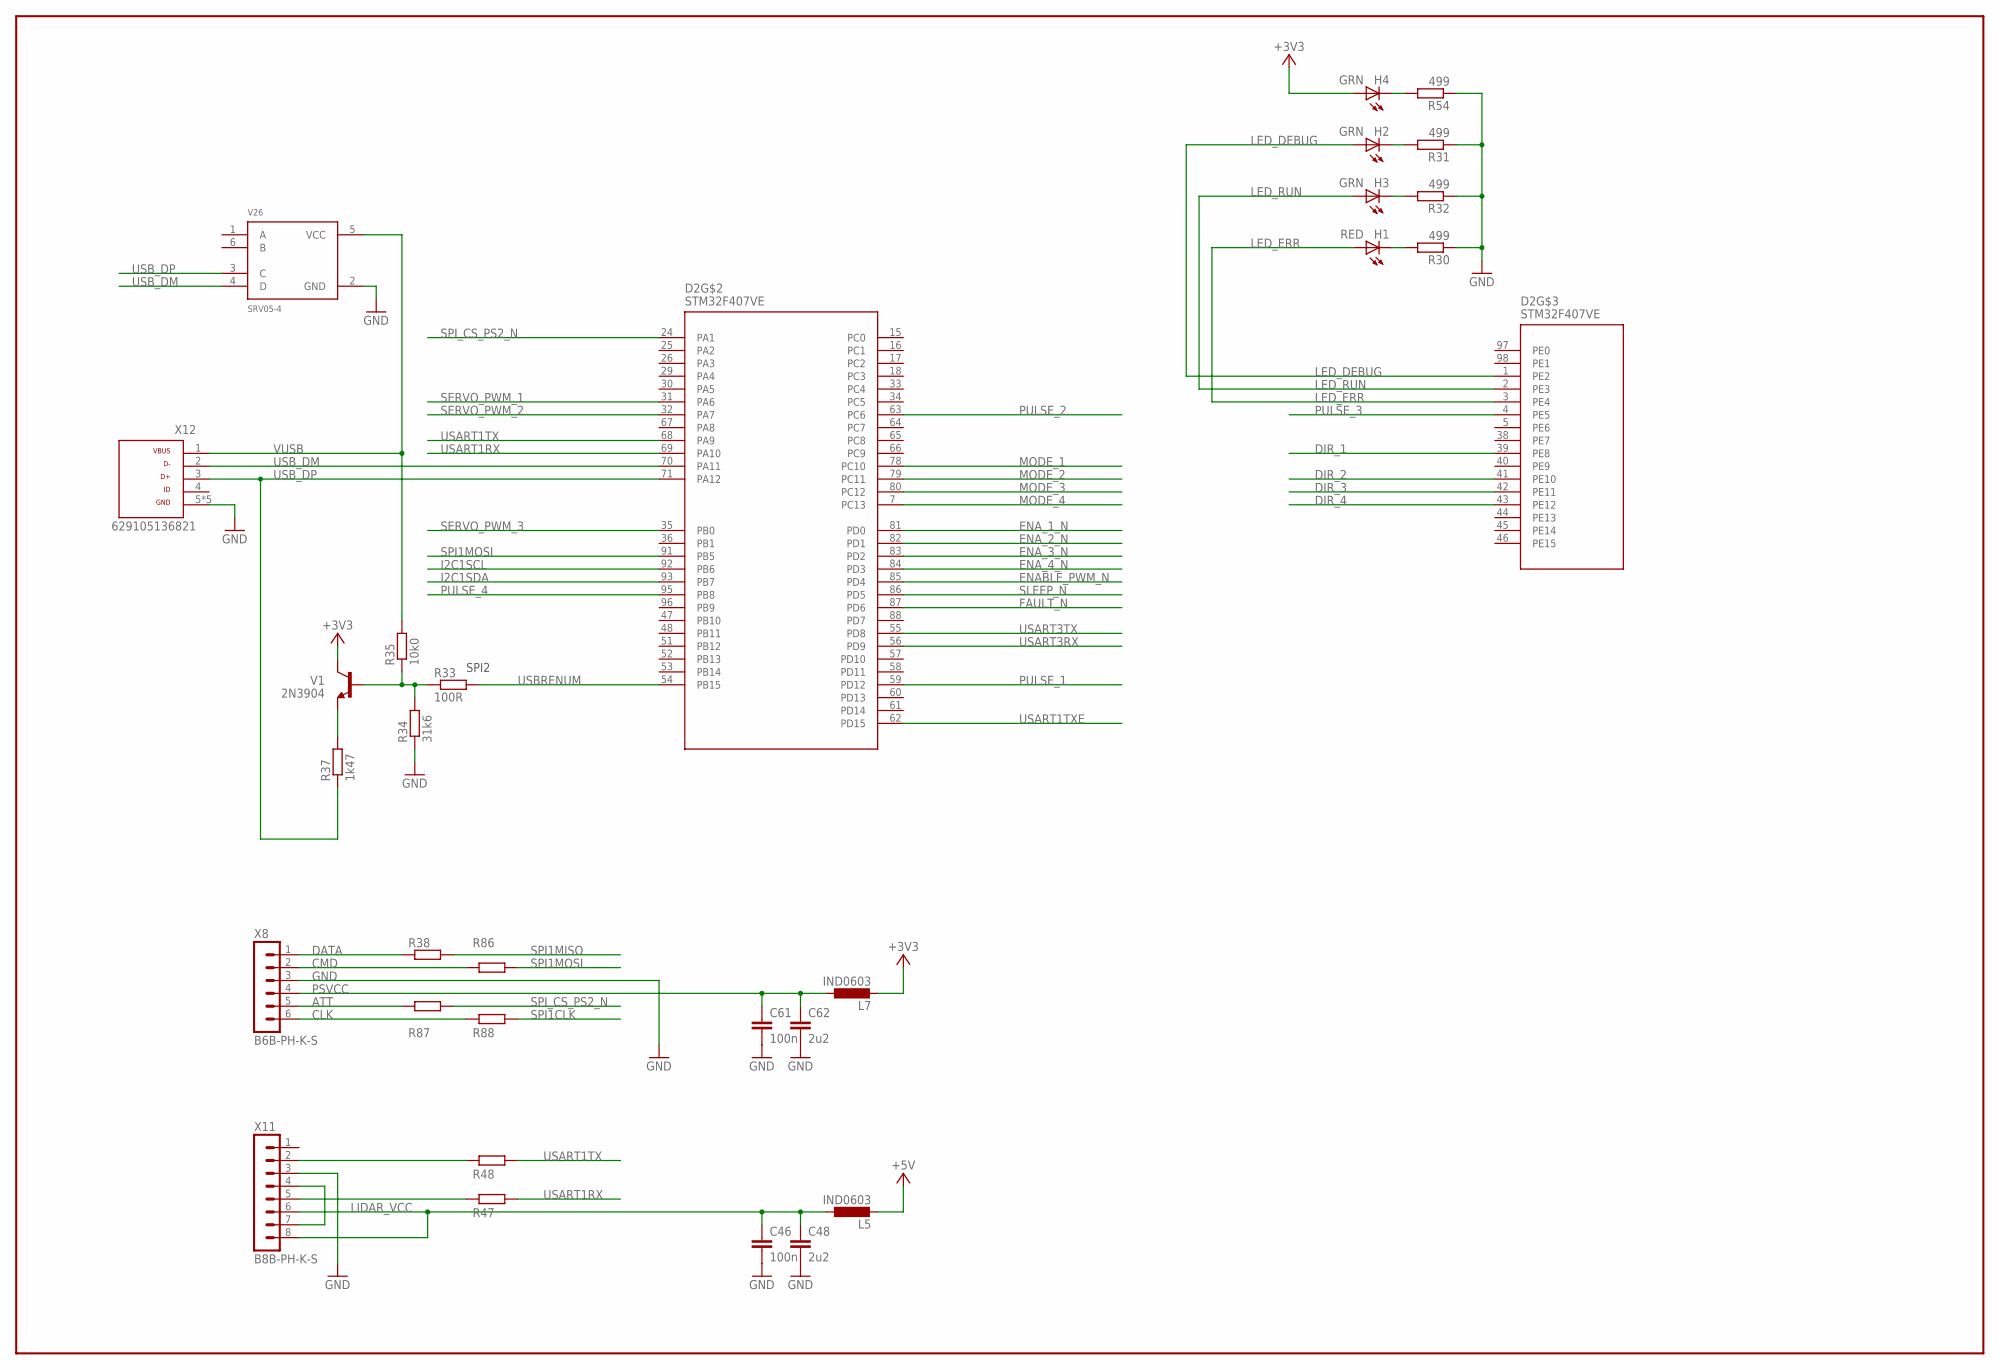
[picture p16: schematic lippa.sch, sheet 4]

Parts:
C46, C61: 100n; C0603
C48, C62: 2u2; C0603
D2: STM32F407VE; LQFP-100
H1: RED; CHIP-LED0603
H2, H3, H4: GRN; CHIP-LED0603
L5, L7: IND0603; R0603
R30, R31, R32, R54: 499; R0603
R33: 100R; PASSIIVIT_R0603
R34: 31k6; PASSIIVIT_R0603
R35: 10k0; PASSIIVIT_R0603
R37: 1k47; PASSIIVIT_R0603
R38, R47, R48, R86, R87, R88: RES0603; OMAT_IC_2_R0603
V1: 2N3904; OMAT_IC_2_SOT23
V26: SRV05-4; OMAT_IC_2_SOT23-6
X8: B6B-PH-K-S
X11: B8B-PH-K-S
X12: 629105136821

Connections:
+3V3: H4.A, L7.2, V1.3 (C); also elsewhere on the board
+5V: L5.2; also elsewhere on the board
ATT: R87.1, X8.5
CLK: R88.1, X8.6
CMD: R86.1, X8.2
DATA: R38.1, X8.1
DIR_1: D2.39 (PE8); also elsewhere on the board
DIR_2: D2.41 (PE10); also elsewhere on the board
DIR_3: D2.42 (PE11); also elsewhere on the board
DIR_4: D2.43 (PE12); also elsewhere on the board
ENABLE_PWM_N: D2.85 (PD4); also elsewhere on the board
ENA_1_N: D2.81 (PD0); also elsewhere on the board
ENA_2_N: D2.82 (PD1); also elsewhere on the board
ENA_3_N: D2.83 (PD2); also elsewhere on the board
ENA_4_N: D2.84 (PD3); also elsewhere on the board
FAULT_N: D2.87 (PD6); also elsewhere on the board
GND: C46.2, C48.2, C61.2, C62.2, R30.1, R31.1, R32.1, R34.1, R54.1, V26.2 (GND), X8.3, X11.3, X12.5, X12.Z1 (5), X12.Z2 (5), X12.Z3 (5), X12.Z4 (5); also elsewhere on the board
I2C1SCL: D2.92 (PB6)
I2C1SDA: D2.93 (PB7)
LED_DEBUG: D2.1 (PE2), H2.A
LED_ERR: D2.3 (PE4), H1.A
LED_RUN: D2.2 (PE3), H3.A
LIDAR_VCC: C46.1, C48.1, L5.1, X11.6, X11.8
MODE_1: D2.78 (PC10); also elsewhere on the board
MODE_2: D2.79 (PC11); also elsewhere on the board
MODE_3: D2.80 (PC12); also elsewhere on the board
MODE_4: D2.7 (PC13); also elsewhere on the board
unnamed: H4.C, R54.2
unnamed: H2.C, R31.2
unnamed: H1.C, R30.2
unnamed: H3.C, R32.2
unnamed: R33.1, R34.2, R35.1, V1.1 (B)
unnamed: R37.2, V1.2 (E)
unnamed: X11.4, X11.7
unnamed: R48.1, X11.2
unnamed: R47.1, X11.5
PSVCC: C61.1, C62.1, L7.1, X8.4
PULSE_1: D2.59 (PD12); also elsewhere on the board
PULSE_2: D2.63 (PC6); also elsewhere on the board
PULSE_3: D2.4 (PE5); also elsewhere on the board
PULSE_4: D2.95 (PB8); also elsewhere on the board
SERVO_PWM_1: D2.31 (PA6); also elsewhere on the board
SERVO_PWM_2: D2.32 (PA7); also elsewhere on the board
SERVO_PWM_3: D2.35 (PB0); also elsewhere on the board
SLEEP_N: D2.86 (PD5); also elsewhere on the board
SPI1CLK: R88.2; also elsewhere on the board
SPI1MISO: R38.2; also elsewhere on the board
SPI1MOSI: D2.91 (PB5), R86.2
SPI_CS_PS2_N: D2.24 (PA1), R87.2
USART1RX: D2.69 (PA10), R47.2
USART1TX: D2.68 (PA9), R48.2
USART1TXE: D2.62 (PD15)
USART3RX: D2.56 (PD9); also elsewhere on the board
USART3TX: D2.55 (PD8); also elsewhere on the board
USBRENUM: D2.54 (PB15), R33.2
USB_DM: D2.70 (PA11), V26.4 (D), X12.2
USB_DP: D2.71 (PA12), R37.1, V26.3 (C), X12.3
VUSB: R35.2, V26.5 (VCC), X12.1

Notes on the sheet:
SPI2

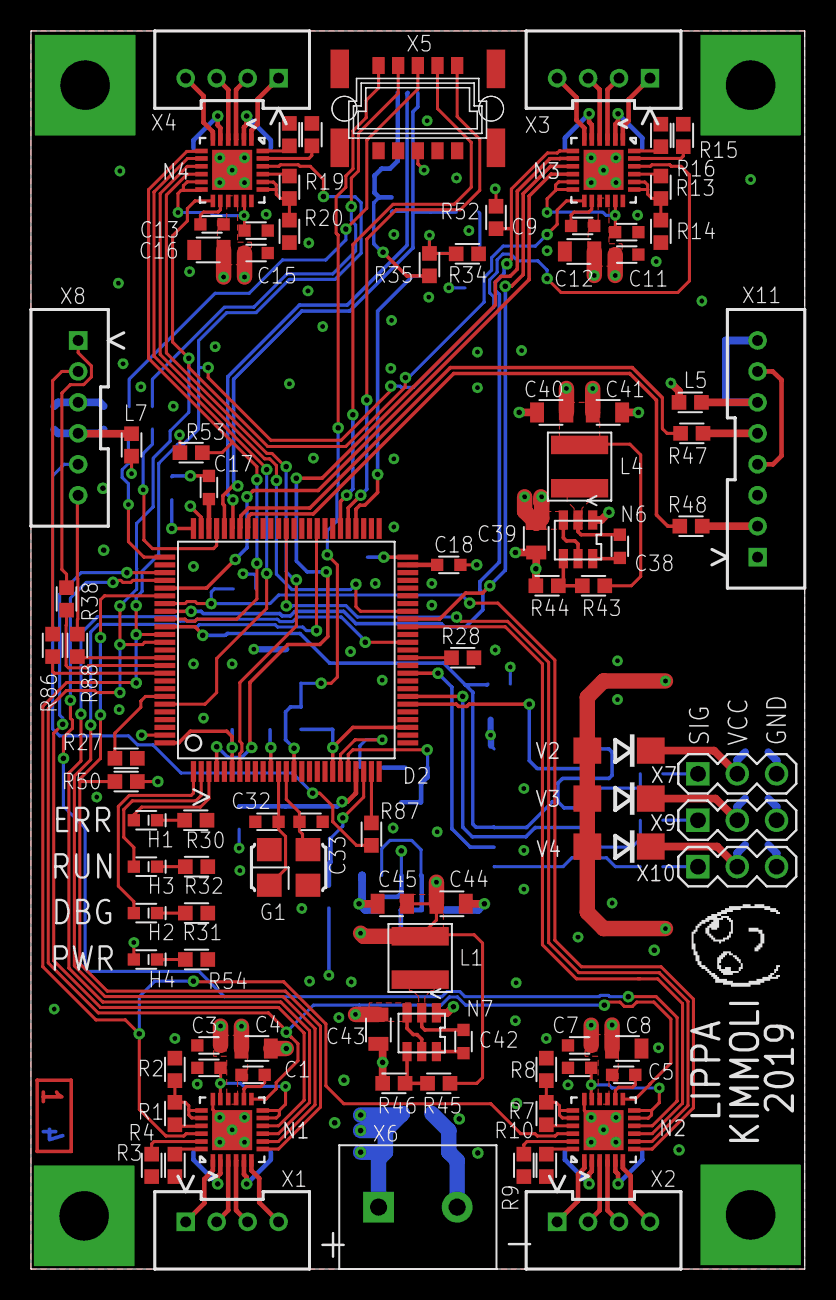
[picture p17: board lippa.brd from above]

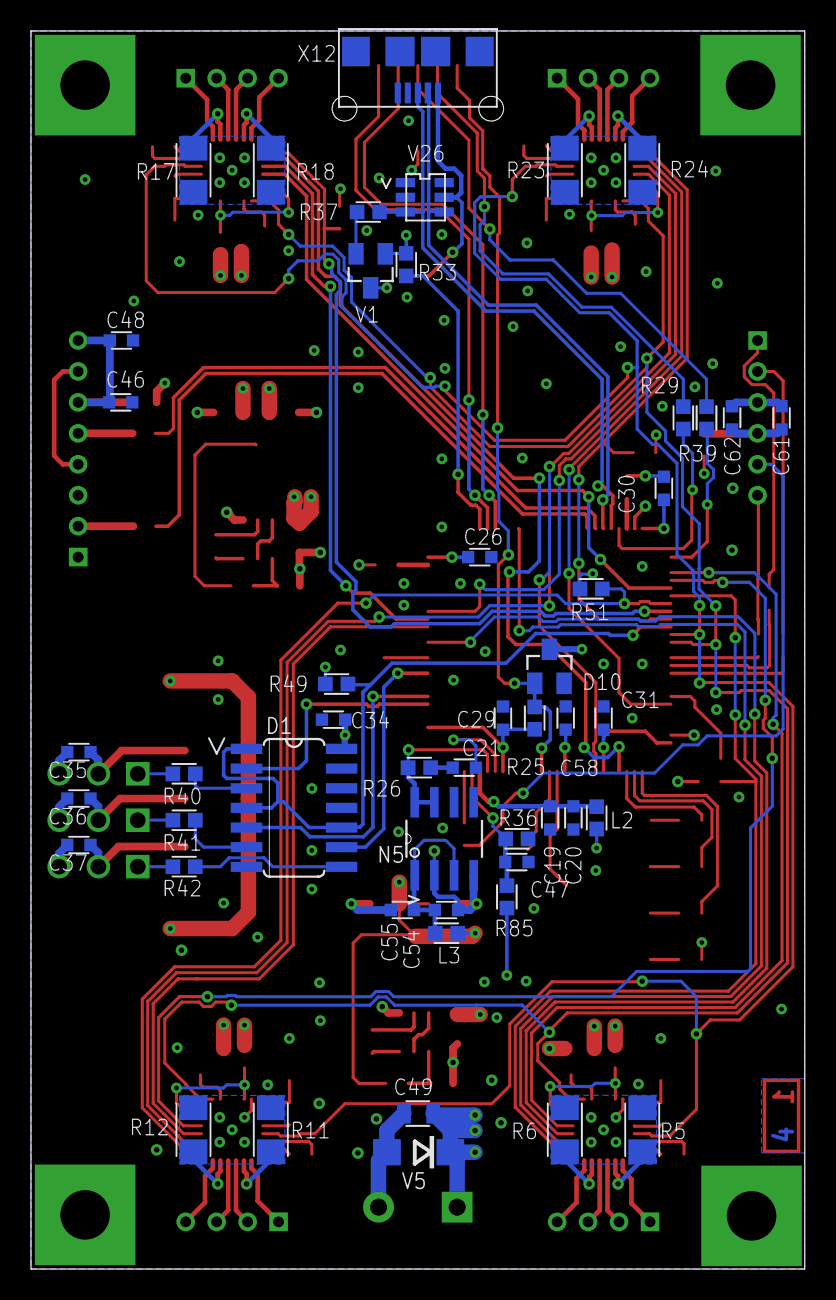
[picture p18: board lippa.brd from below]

Board: 4 copper layers, 50.0 x 80.0 mm, 150 parts (50 on the bottom side), 135 nets.

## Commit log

2019-04-25 initial design, nothing complete
    [lippa.brd, lippa.sch]
2019-04-27 more wip
    [lippa.brd, lippa.sch]
2019-04-27 almost done
    [lippa.brd, lippa.sch]
2019-04-28 Layout complete
    [lippa.brd, lippa.sch]
